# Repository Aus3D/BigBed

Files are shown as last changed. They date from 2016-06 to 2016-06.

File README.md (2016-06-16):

**Please note that BigBed is still in development and is not ready for use - we're in the testing phase right now, and should be ready to go shortly. Thanks for your patience!**

# Aus3D BigBed

BigBed is an open-source PCB heated-bed for RepRap 3D printers. It is based on [earlier PCB heated bed designs](http://reprap.org/wiki/PCB_Heatbed), but incorporates several key improvements. It features many of the same design choices from the popular MK2, MK2b and MK3 open-source heated beds, and should feel quite familiar to anyone who has used one of those designs before.

# Key Features
## Edge Temperature Correction 
Both E3D and Prusa Printers have announced new heated beds that make use of variable trace width to 'regulate' the amount of heat generated by different regions of the heated bed. This allows the outer edges of the PCB to maintain a much closer temperature to the centre, whereas with previous designs there was often a non-trivial temperature difference.

Unfortunately, at the time of writing, neither option is open source, and both can only be obtained as part of their respective 3D printer kits. While it is likely that both companies will release open-source designs at some point in the future (due to their strong history of contributing to the RepRap community), this means there is no readily available option at present for those building their own printers, or looking to upgrade machines they already have.

## SMD Thermistor
Most PCB heated beds require a separate wired thermistor to be attached to the bed in order to monitor the temperature. The BigBed features pads for an 0603 SMD thermistor, and pins near the power connectors through which it can be wired. This should make wiring easier and removes the need to secure an external thermistor to the bed (which is usually done using Kapton tape).

## Pluggable Connectors
The previous designs (MK2 et. al) require the user to directly solder the power wires to the heated bed. While this works fine for power transmission, the inability to disconnect the wires easily can be annoying in some situations (maintenance, cable-management, etc.).

To address this, the BigBed takes a cue from E3D's Varipower bed and adds pins for suitable Molex connectors that can be used to carry both power and the thermistor signal back to the printers' control board. Molex Micro-Fit connectors were chosen due to their small-footprint, good mechanical strength (to resist cable strain on moving beds) and relatively high current-carrying capacity.

The BigBed has room for two of these connectors, where one connects the board in a 12V configuration and the other in a 24V configuration. We have cables available that match with these connectors and provide suitable plugs for most control boards on the other end.

We don't want to exclude anyone though, so the large pads used for directly soldering wires on earlier PCB heated beds are still present - feel free to directly attach wires if that's the best solution for your printer.

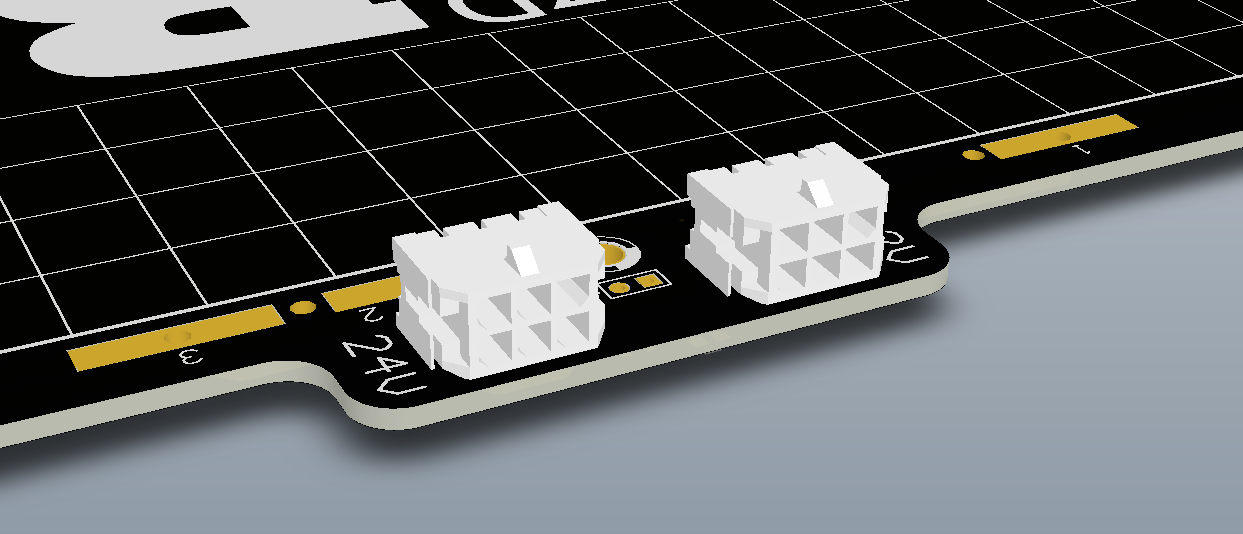
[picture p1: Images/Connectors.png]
Connectors

## Big!
BigBed isn't the biggest bed out there - and yes, we know, "But it's called BigBed!". 

BigBed has a print area of 240x240mm, which is intended to be a healthy improvement over it's predecessor's 200x200mm print areas. Larger sizes become difficult to heat without stressing 12V power supplies, or overheating the control board's MOSFET. Additionally, larger sizes start to become unwieldly for printers that use a moving print-bed (including i3-based printers, etc.), due to the increased mass of the bed - resulting in either decreased print speed or lower-quality prints. 

BigBed's size was selected to provide an optimum between print volume, electronics compatibility, and print quality.

#Dimensions and Mounting
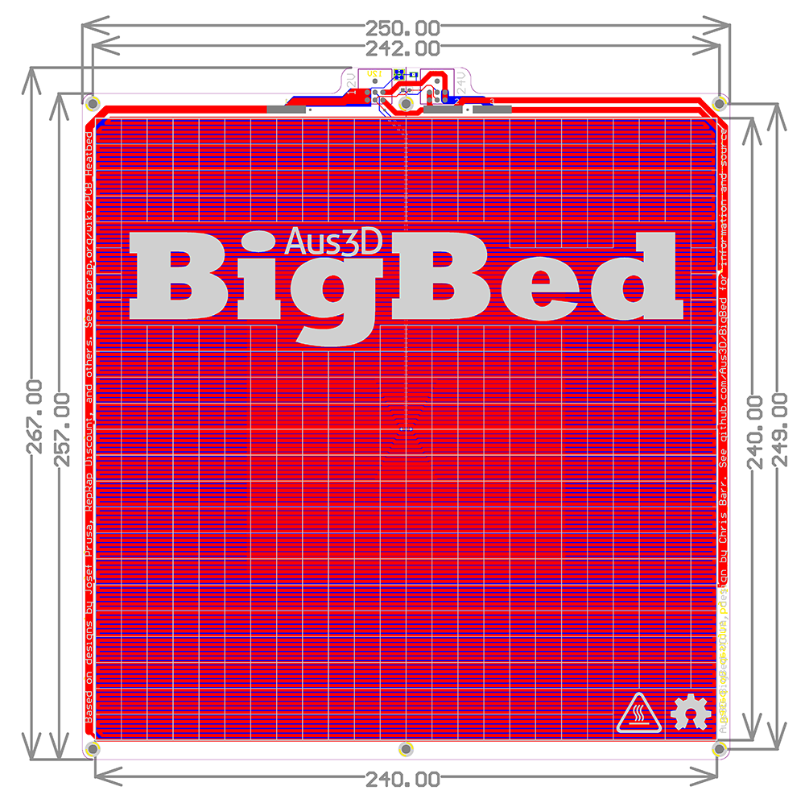
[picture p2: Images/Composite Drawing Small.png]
Dimensions


#Where to Buy
Once we've got the design thoroughly tested and are happy that everything is working smoothly, we'll have these boards up for sale on the [Aus3D](http://aus3d.com.au/) website.

# Open Source
In the spirit of the RepRap project, BigBed is fully open source - files to manufacture or modify a board of your own are included in this repository. BigBed is licensed under a GPLv3 license, and anyone is free to modify it, manufacture it, sell it - as long as you share your modifications under the same license, we're good!

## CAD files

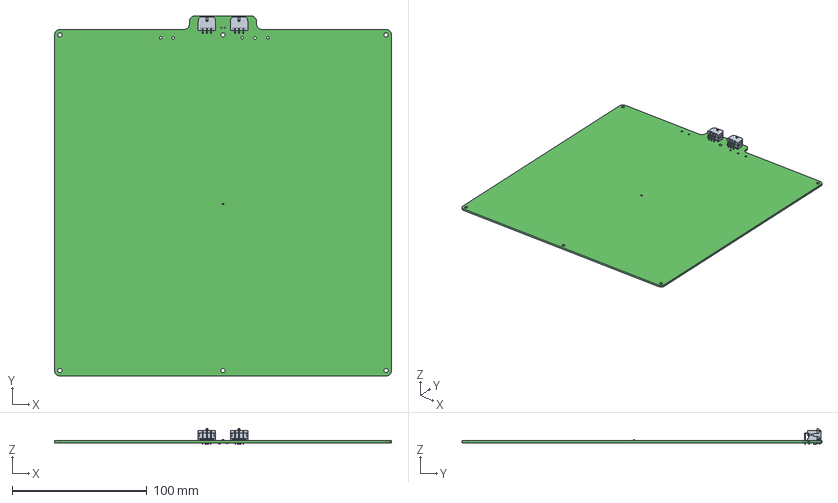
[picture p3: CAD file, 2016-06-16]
BigBed.step
250.0 x 267.0 x 11.9 mm
Board
RES_0805_(2012_metric)
Extruded x 8
RES_0603_(1608_metric)

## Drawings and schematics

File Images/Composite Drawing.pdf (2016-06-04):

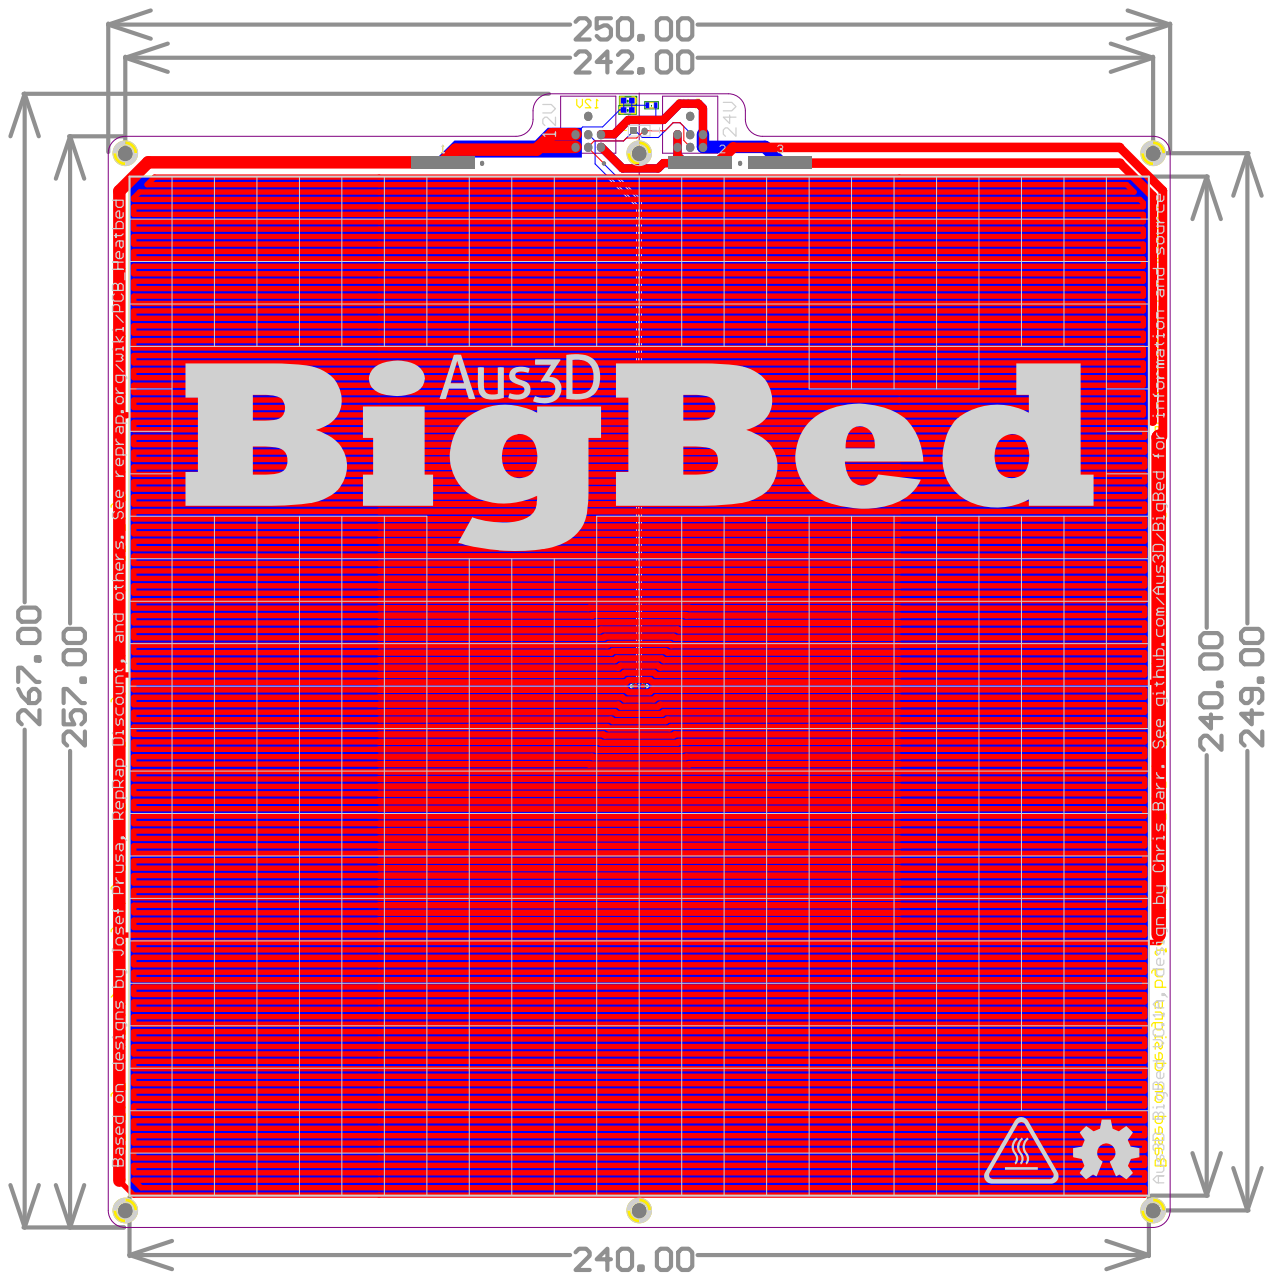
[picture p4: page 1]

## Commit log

2016-06-04 V0.2A
    Resized board width to 250mm, down from 255mm. Some trace sizes and positions changed to suit.
    Should make board easier to use, take up less space etc.
    [BigBed.GBL, BigBed.GBO, BigBed.GBP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]
2016-06-04 Connector Image
2016-06-16 3D Step File
    [BigBed.step]
2016-06-29 Plane as power rails
    [BigBed.PcbDoc, BigBed.SchDoc]
2016-06-29 Board Resize
    [BigBed.PcbDoc]
2016-06-30 V0.3A
    Extend heating traces outside print bounds to minimise cold edges.
    Adjust heating trace thicknesses to increase power draw slightly.
    Move thermistor to opposite side from heating traces, so traces can face upwards into print surface.
    Rework connectors / pads to improve current carrying capacity / reduce self-heating.
    [BigBed.GBL, BigBed.GBO, BigBed.GBP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]
2019-05-20 V0.4
    Committing old files
    [BigBed.PcbDoc]
2019-05-20 Remove unneeded files
    [BigBed.GBL, BigBed.GBO, BigBed.GBP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]
